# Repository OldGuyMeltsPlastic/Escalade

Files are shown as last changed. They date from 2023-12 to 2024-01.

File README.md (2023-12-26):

# Escalade (French for "climb", specifically mountain climbing)

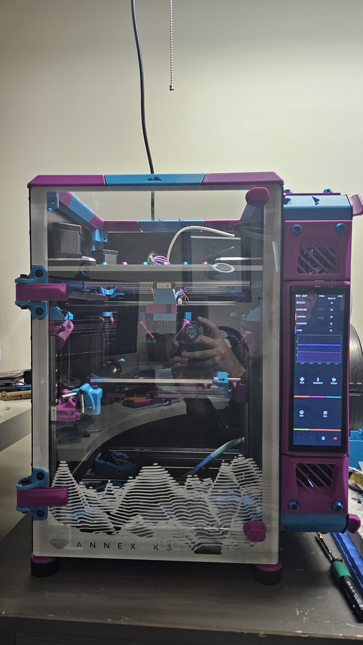
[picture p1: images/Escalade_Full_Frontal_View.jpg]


Escalade is an Annex Engineering K3 printer with a few twists, just because I can.

After attending the Rocky Mountain Rep Rap Festival (RMRRF) in Loveland, CO in April 2023, I came back home to Ottawa, Canada and ordered myself a K3 kit from Fabreeko.

Fabreeko had a K3 on display at their booth, and the design and overall build quality just blew me away.
Another attendee @OB1Kenobi from the Annex Engineering Discord server, had also brought his own K3 build to the event, and he had a sidepack mounted on the right with a Waveshare 7.9" HDMI display mounted vertically.
I was inspired to do something similar with my own K3 build.

I have created a K3 playlist on my YouTube channel and documented most of the physical build there:
https://www.youtube.com/playlist?list=PLngLOesYVWnwKW8zaA5v_0eK2fdAM9LTv<br>
I have also created a build log on the Annex Engineering Discord server here:
https://discord.com/channels/641407187004030997/1180948550843117720

```
Original K3 configuration:

|------------------------|
|        BACKPACK        |
|------------------------|
| Y  |    | Z1 |    | X1 |
|-----    ------    -----|
|                        |
| ------          ------ |
| | Z  |          | Z2 | |
| ------          ------ |
|-----              -----|
| X  |              | Y1 |
|------------------------|

My K3 configuration:

|------------------------|----|
| Y  | Z  |         | X1 |    |
|----------         |----|    |
|                        |    |
|                 ------ |SIDE|
|                 | Z1 | |PACK|
|                 ------ |    |
|----------         -----|    |
| X  | Z2 |         | Y1 |    |
|------------------------|----|
```

For my build, it wasn't enough to rotate the printer so that the backpack now sits on the right side, but I also ended up swapping the X and Y axes so that X still moves left to right, and Y still moves front to back in the rotated configuration.

To be clear, the back/sidepack still sits on the original rear side of the printer, but the front door has been moved right, replacing the original right panel, and the right panel has moved left, replacing the original front door.

My configuration with the stock toolhead has a Phaetus Dragon UHF hotend, a Beacon Rev D probe, and a K3rabiner toolhead PCB. The mount parts that I found for this toolhead configuration move the hotend cooling fan to the "back" of the hotend, which leaves the front of the hotend more easily accessible for removing the silicone sock and/or swapping nozzles. Printed parts required for this toolhead configuration were collated by @ChristianN on the Annex Engineering Discord Server here: https://discord.com/channels/641407187004030997/1139276599645179946

I sourced a Waveshare 7.9" DSI display, instead of the Waveshare 7.9" HDMI display. The screw holes configuration to mount the DSI and HDMI are different from each other. I ended up having to take Minsekt's original HDMI display mount, and as no CAD was available, I hacked it apart in PrusaSlicer to get something close to functional for my DSI display.
Minsekt's mount for Waveshare 7.9" HDMI displays: https://github.com/Annex-Engineering/Annex-Engineering_User_Mods/tree/main/Printers/K3/Minsekt-K3_WaveshareScreen
OGMP's mount for Waveshare 7.9" DSI displays: https://www.printables.com/model/691631-annex-engineering-k3-sidepack-waveshare-79-dsi-mou

I am using an Arducam IMX519 Pi Cam V3-compatible camera connected to the Raspberry Pi 4B via FFC. I used Ryan-G's Outside Camera Mod and airox's rpi camera mod to mount it in the sidepacks large top middle grommet hole.
https://github.com/Annex-Engineering/Annex-Engineering_User_Mods/tree/main/Printers/K3/Ryan_G-K3_Outside_Camera
https://github.com/Annex-Engineering/Annex-Engineering_User_Mods/tree/main/Printers/K3/airox-rpi-mount-for-camera-mod-ryan

I also had to adjust the positions of the Z-Tilt probe points accordingly. Note that the Z motors and bed assembly retain their original mount points per a stock build.

Also, when mounting the front door panel to the hinges, the build instructions recommended using an M3 SHCS and a 1 mm washer/spacer inside the door panel. I found that this would cause the Z2 kinematic bed mount, which now sits at the front left of my build space, to bump into those screws at the bottom of the door, so I replaced the M3 SHCS + washer with an M3 BHCS and no washer. The door is just as secure, but now the Z2 kinematic bed mount has clearance to move up and down unobstructed.

While the K3 is now printing, I am working through resolving some pretty bad print artifacts that appear to be caused by a physical problem with the gantry motion system. Once I have corrected these, I will share my configuration and slicer settings for reference.

To mount the electronics in my K3 sidepack, I asked my friend Fizzy, creator of the Electronics Mounting System (EMS) that is popular with many Voron printer builders, to create an EMS frame for the K3. I will update with a link to it here once he has published it on Printables.

Many thanks to all of the greatly helpful people on the Annex Engineering and Fabreeko Discord servers for all of their assistance and timely responses to my many questions. This printer build would have been much more work on my part without all of the help that I received.

Photos:<br>

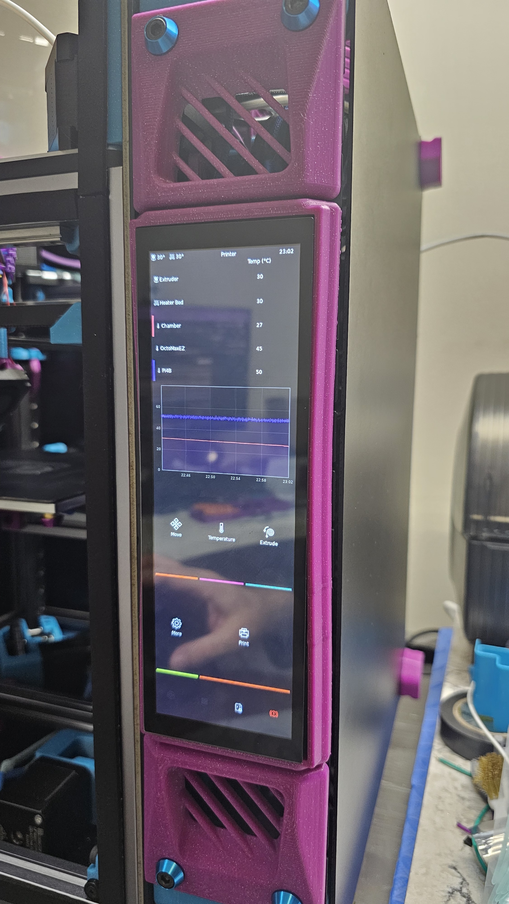
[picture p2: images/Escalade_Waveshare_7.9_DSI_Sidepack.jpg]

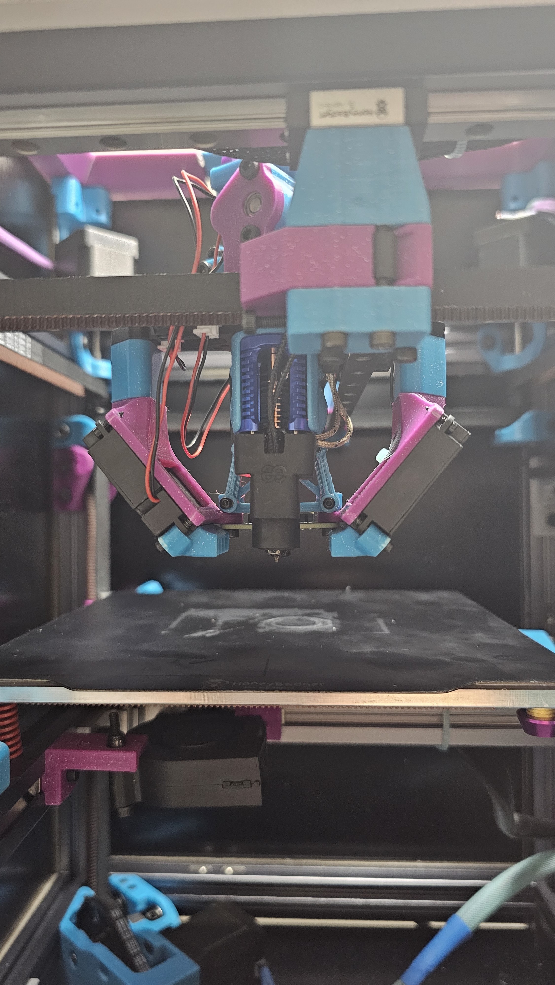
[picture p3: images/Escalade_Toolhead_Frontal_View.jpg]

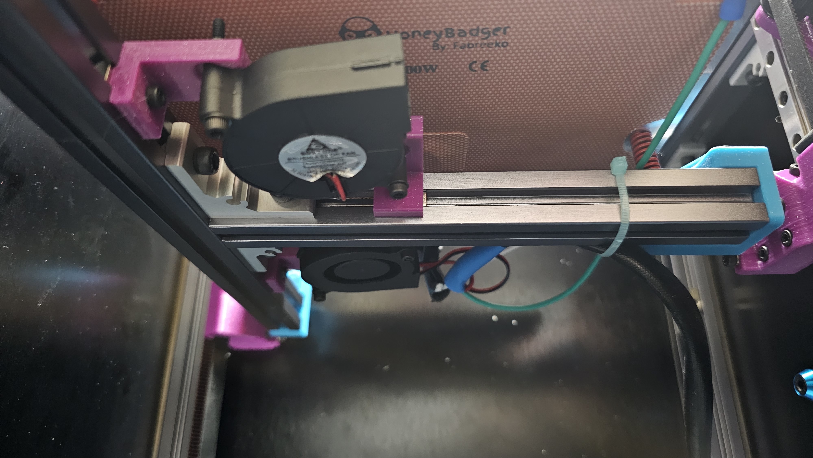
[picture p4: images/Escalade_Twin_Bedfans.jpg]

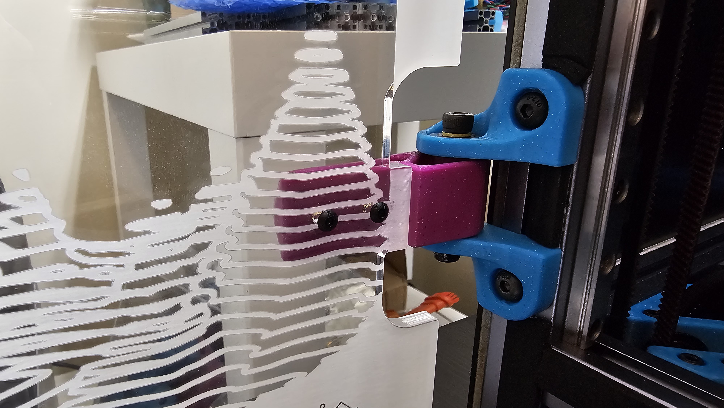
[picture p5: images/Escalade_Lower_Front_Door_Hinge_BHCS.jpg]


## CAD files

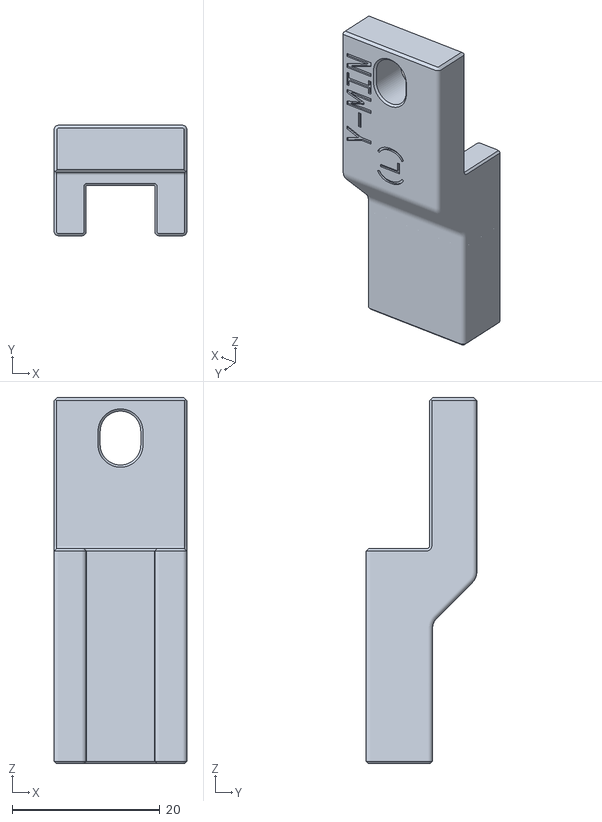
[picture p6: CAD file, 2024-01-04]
mods/STLs/OGMP_longer_y_min_left_split corner_endstop_x1_rev5.stl
18.0 x 15.0 x 49.6

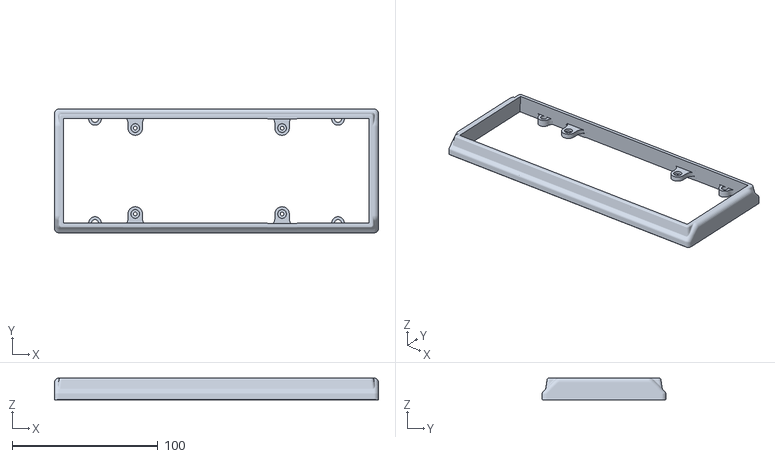
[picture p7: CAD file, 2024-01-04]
mods/STLs/OGMP_Waveshare_7.9_DSI_Frame_K3_Standard.stl
222.5 x 85.0 x 15.0

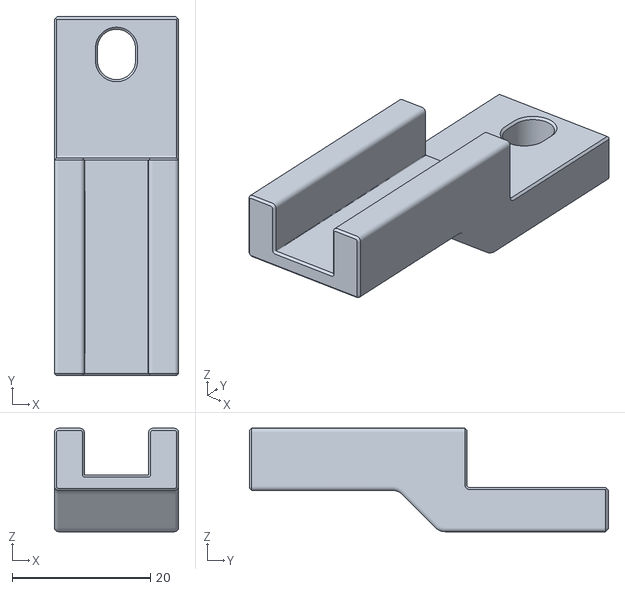
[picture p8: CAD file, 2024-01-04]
mods/STLs/OGMP_longer_x_min_split_corner_endstop_x2_rev5.stl
18.0 x 52.0 x 15.0

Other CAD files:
mods/STLs/OGMP_K3_nozzle_fan_left.stl
mods/STLs/OGMP_longer_y_min_right_split corner_endstop_x1_rev5.stl
